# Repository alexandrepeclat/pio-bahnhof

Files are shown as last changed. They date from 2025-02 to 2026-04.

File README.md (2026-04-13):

### TODO SOFTWARE :

```
TODO MQTT + HomeAssistant ?
TODO virer les deps inutiles (CRC32 utilisé par librairie)
 TODO voir pour les conflits avec dépendances de command-library
 TODO réorganiser la détection d'erreurs.
- on a emergencyStop et assertThis un peu interchangeables
- on a des checks sur des getters ou à des moments dans la logique du code et dans les fonctions dédiées...
- le state, flag et message sont un peu redondants
 TODO passer les strings en mémoire flash plutôt qu'en RAM 
 TODO s'assurer que tous les "getters" utilisés notamment dans les debug ne change pas les états ou valeurs :-)
 TODO Vérifier les valeurs passées depuis l'api un peu mieux en terme de limites
 TODO sécuriser API ?
```

### Flash to board

- Flash the software : `pio run --target upload`
- Flash static html file : `pio run --target uploadfs`

### Setting up the pulse offset

- Do manual calibration
- Set default panel as the actual panel
    - You should have the same panel on the device and UI
- Move pulse by pulse until the panel changes on the device
    - You may have a different panel on the device and UI
- Tune the pulse offset until both device and UI are on the same panel
    - If the UI shows the next panel : increase pulse offset
    - If the UI shows the previous panel : decrease pulse offset
- Save the settings !

### Hardware

| Ref | Description | V(in) | V(out) | Datasheet |
| --- | --- | --- | --- | --- |
| LM2596 | Step-down voltage regulator (Buck converter) | 7-30V | 5.2V | https://www.ti.com/product/LM2596 |
| NodeMCU v3 | ESP8266 module | 5-9V | | https://github.com/nodemcu/nodemcu-devkit-v3.0 |
| 38S6G5 | Optical encoder (360 steps/rev * 4 pulses) | 5-24V | | https://www.mantech.co.za/Datasheets/Products/e38s_jz-yeba.pdf |
| MG996R | Continuous rotation servo motor | 4.8-6.6V | | https://www.towerpro.com.tw/product/mg996r |
| KY-010 | Optical sensor | 3.3-5V | | https://sensorkit.joy-it.net/fr/sensorsky-010 |

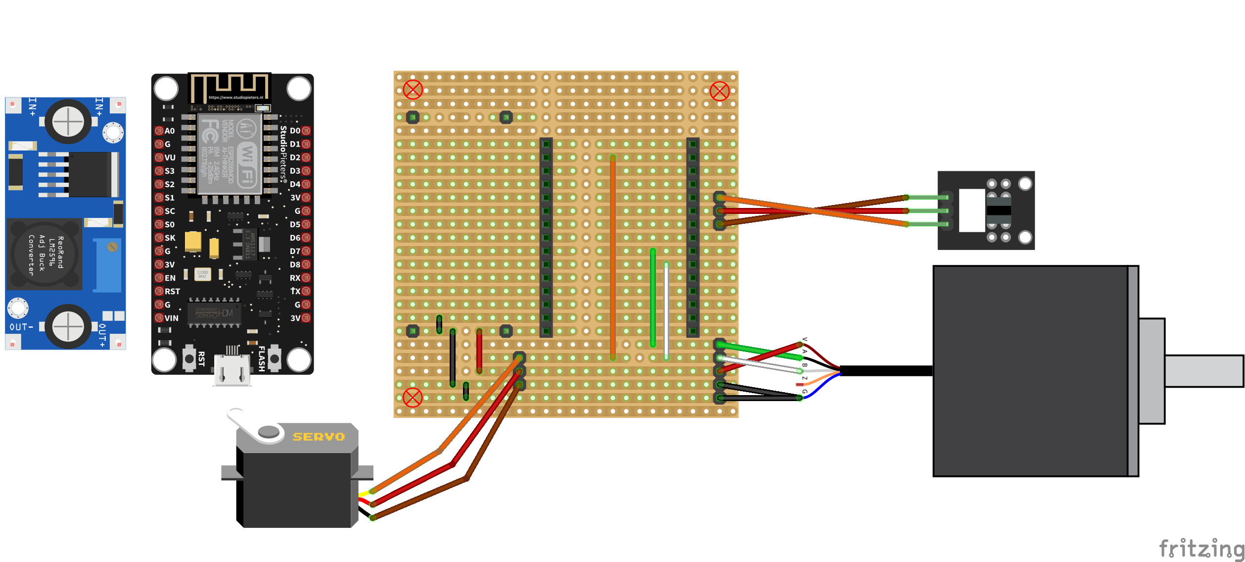
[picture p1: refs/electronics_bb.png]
Breadboard scheme

Electro scheme

### Mechanical stuff

https://geargenerator.com/beta/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

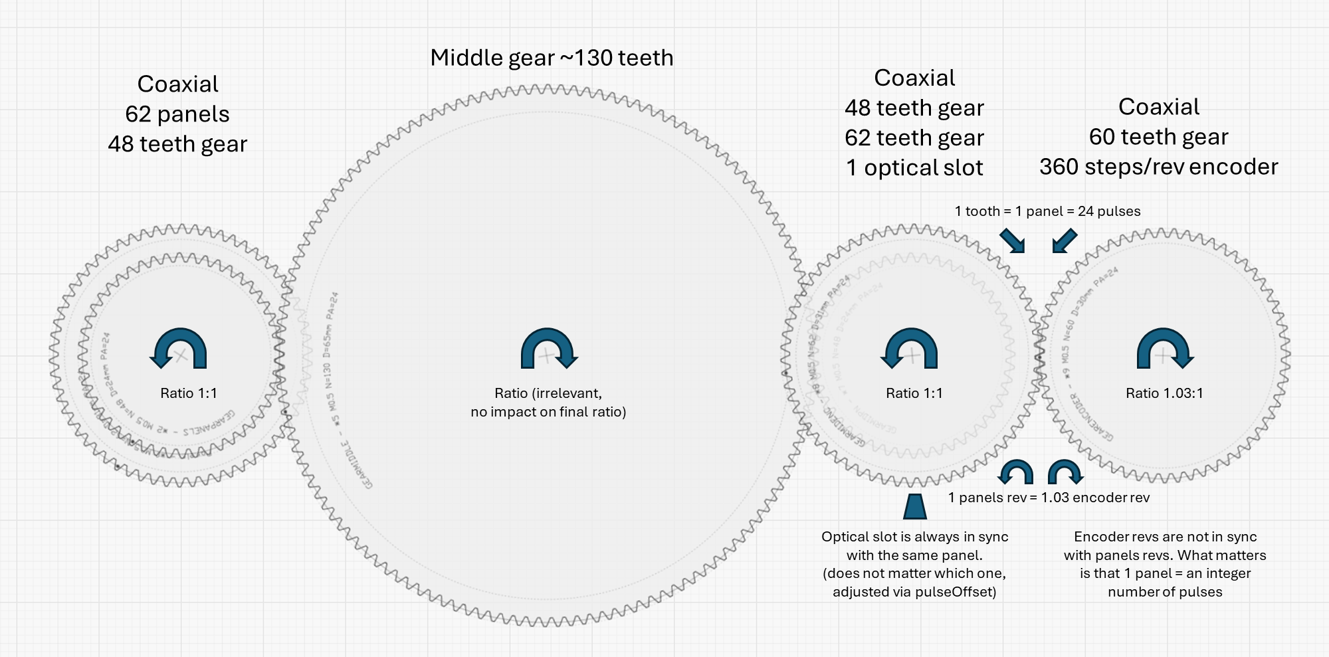
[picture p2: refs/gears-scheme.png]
Gears scheme


> Notes : 
>
> - Pulses number / panel must be an integer. This is why we have "clean" number of teeth for both gears, related to what is connected to them : 
> - 62 teeth for panels (divisor of 62 panels, but could be 31, 124...)
> - 60 teeth for encoder (divisor of 360 steps, but could be 36, 40, 72)
> - The actual pulses number per panel is `360 steps / rev * 4 pulses / step * (1 / 60 rev) = 24 pulses / panel`
> - However we do not need to have 1 panels full revolution to be equal to 1 encoder revolution
> - The actual encoder speed is `60/62 = 0.96` of the panels speed 
> - For each panels full revolution, we have `62/60 = 1.0333` encoder revolutions

### REST call examples

```
curl -Method Get -Uri "http://192.168.0.222/stop"
curl -Method Get -Uri "http://192.168.0.222/panel"
curl -Method Post -Uri "http://192.168.0.222/moveToPanel" -Body @{panel=6} -ContentType "application/x-www-form-urlencoded"
curl -Method Post -Uri "http://192.168.0.222/advancePanels" -Body @{count=2} -ContentType "application/x-www-form-urlencoded"
curl -Method Post -Uri "http://192.168.0.222/setCurrentPanel" -Body @{panel=0} -ContentType "application/x-www-form-urlencoded"
```

### Useful doc

- Split flap wall decoration SBB/CFF : https://commerce.sbb.ch/en/split-flap-display-wall-decoration-different-special-trains-1100.html
- Projet split flap diy : https://github.com/davidkingsman/split-flap
- Lib encoder esp32 (multi modes dont quadrature, avec interruptions) : https:github.com/madhephaestus/ESP32Encoder 
- Exemple encoder (pas quadrature mais directionnel) : https:github.com/sandy9159/How-to-connect-optical-rotary-encoder-with-Arduino
- Lib encodeur RPi Pico : https://github.com/GitJer/Some_RPI-Pico_stuff/tree/main/Rotary_encoder
- Lib encodeur interruptions : https://github.com/gfvalvo/NewEncoder/tree/master
- Connexion encodeur optique esp32 : https://electricdiylab.com/how-to-connect-optical-encoder-with-esp32/#Wiring_of_Optical_encoder_and_ESP32
- Thread sur lecture encodeur rapide : https://forum.arduino.cc/t/arduino-and-high-speed-rotary-encoders/327931/7
- Thread lecture encodeur state table : https://forum.arduino.cc/t/reading-a-quad-encoder-and-converting-to-a-function/272506/2
- Thread encodeur interruptions : https://stackoverflow.com/questions/51297371/arduino-rpm-code-with-quadrature-encoder-600ppr

### Shitty issues 

- Optical encoder 38s6g5 needs >= 5V https://forum.arduino.cc/t/fyi-interfacing-e38s6g5-600b-g24n-600p-r-rotary-encoder/1057892
- noInterrupt() et interrupt() pas utilisés car perturbent la lecture Serial et serveur HTTP. En principe on en a pas besoin car les variables volatiles sont <= 32 bits donc atomiques sur ESP8266.
- EEPROM.read() and EEPROM.write() only work with 1 single byte. Need to use EEPROM.get() / EEPROM.set() for int.

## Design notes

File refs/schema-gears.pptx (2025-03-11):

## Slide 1

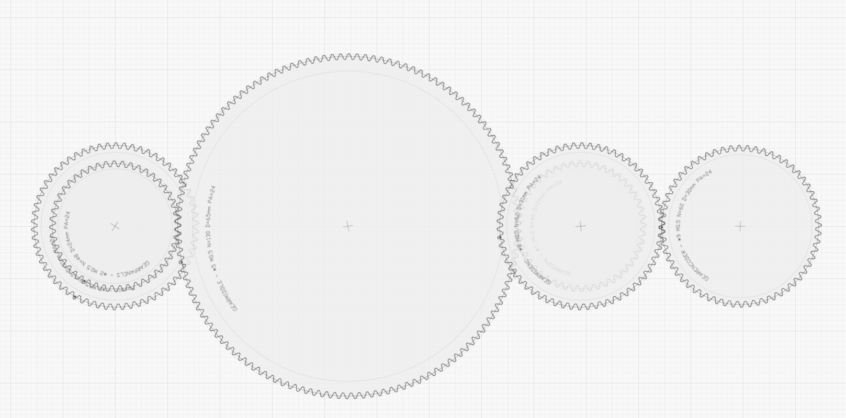
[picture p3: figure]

Coaxial
62 panels
48 teeth gear

Middle gear ~130 teeth

Coaxial
48 teeth gear
62 teeth gear
1 optical slot

Coaxial
60 teeth gear
360 steps/rev encoder

1 tooth = 1 panel = 24 pulses

Ratio 1:1

Ratio 1:1

Ratio (irrelevant,
no impact on final ratio)

Ratio 1.03:1

1 panels rev = 1.03 encoder rev

Optical slot is always in sync with the same panel.
(does not matter which one, adjusted via pulseOffset)

Encoder revs are not in sync with panels revs. What matters is that 1 panel = an integer number of pulses

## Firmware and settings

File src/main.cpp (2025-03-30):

#define DEBUG_ENABLED

#include <DebugBuilder.h>
#include <EEPROM.h>
#include <ESP8266WiFi.h>
#include <ESP8266mDNS.h>
#include <ESPAsyncWebServer.h>
#include <JsonSettingsBase.h>
#include <LittleFS.h>
#include <RestCommandHandler.h>
#include <SerialCommandHandler.h>
#include <Servo.h>
#include <secrets.h>

enum AppState {

  /**
   * Stopped state after an issue is detected.
   */
  EMERGENCY_STOPPED,

  /**
   * Normal stopped (idle) state.
   */
  STOPPED,

  /**
   * Auto-calibrating. Will move to target panel afterward.
   */
  AUTO_CALIBRATING,

  /**
   * Manually calibrating. Will stop afterward.
   */
  CALIBRATING,

  /**
   * Moving to target panel at normal speed.
   * Will auto-calibrate if not already done, then return to this state.
   * Will stop when target is reached.
   */
  MOVING_TO_TARGET,

  /**
   * Moving to target panel at slow speed.
   * Will not try to auto-calibrate.
   * Will stop when target is reached.
   * Used for settings adjustments or debugging.
   */
  MOVING_TO_TARGET_SLOW,
};

// Prototypes declaration
int getCurrentPulse();  // TODO réorganiser les fonctions dans un ordre correct
int getCurrentPanel();
int getTargetPulse();
float calculateSpeedMovingToTarget();
int getRemainingPulses();
void setMotorSpeed(float normalizedSpeed);
void setTargetPanel(int panel);
int getTargetPanel();
void emergencyStop(String message);
String stateToString(AppState state);
void setCurrentState(AppState newState);
int getDefaultPanel();
int getDefaultPulseOffset();
int getCurrentRpm();
float normalizeSpeed(int speed);
int denormalizeSpeed(float normalizedSpeed);
int computePulsesForwardDistance(int from, int to);
int computePulsesMinDistance(int from, int to);
int computeRpm(int lastPulse, int currentPulse, unsigned long lastTime, unsigned long currentTime);

#define DEBUG_ENABLED

// Pins configuration
#define SERVO_PIN D1      // Orange
#define ENCODER_PIN_A D6  // Green
#define ENCODER_PIN_B D7  // White
#define OPTICAL_PIN D4    // Orange

// Connections
AsyncWebServer server(80);  // For REST API calls
AsyncCorsMiddleware cors;
AsyncWebSocket ws("/panel");  // For notifying clients of panel changes
SerialCommandHandler serialCommandHandler;
RestCommandHandler restCommandHandler(server);

// App state
volatile AppState currentState = STOPPED;
bool errorFlag = false;      // Emergency stop flag
String errorMessage = "";    // Emergency stop message
bool criticalError = false;  // Error preventing the device from running //TODO merger avec errorFlag ?
volatile bool calibrated = false;

// Panels and pulses
const int PANELS_COUNT = 62;
const int PULSES_PER_PANEL = 24;                           // ENCODER_RESOLUTION / ENCODER_GEAR_TEETH * ENCODER_PULSES_PER_STEP = 360 / 60 * 4 = 24
const int PULSES_COUNT = PANELS_COUNT * PULSES_PER_PANEL;
const int TARGET_PULSE_OFFSET = 12;                        // When setting a target panel, use the nth pulse of this panel for centering //TODO à voir si configurable (et vitesse aussi car dépend de elle)
static_assert(TARGET_PULSE_OFFSET >= 0 && TARGET_PULSE_OFFSET < PULSES_PER_PANEL, "OFFSET must be in range [0-PULSES_PER_PANEL]");

// Encoder
const int8_t ENCODER_DIRECTION_SIGN = 1; // 1 for normal direction, -1 for reverse (depends on AB wiring)
const int8_t ENCODER_STATE_TABLE[16] = {0, 1, -1, -0, -1, 0, -0, 1, 1, -0, 0, -1, -0, -1, 1, 0};  // Encoder state table for natural debouncing (-0 are non valid states)
int targetPulse = 0;
volatile int encoderPulsesRaw = 0;

// Optical sensor
const int OPTICAL_DETECTED_EDGE = RISING;  // Optical is 0 on slot (detected) and 1 when signal cut by wheel body
volatile bool opticalState = HIGH;         // Assume not on slot at start (will be updated on 1st loop)

// Servo
Servo servo;
const int STOP_SPEED = 90;  
const int RUN_SPEED = 140;  // Servo max forward speed [91-180] (140 is quite good, 6 sec for 1 revolution)
static_assert(RUN_SPEED > 90, "RUN_SPEED must be greater than 90 or everything will break !");

/**
 * Configurable settings stored in flash memory.
 * Values can be preset by flashing a settings.json file on the ESP.
 */
class Settings : public JsonSettingsBase {
 public:
  int defaultPulse = 0;     // Default pulse for the device : 0
  String mdnsName = "cff";  // Default MDNS name for the device : cff.local

  Settings()
      : JsonSettingsBase("/settings.json") {}

  void serialize(JsonDocument& doc) override {
    doc["defaultPulse"] = defaultPulse;
    doc["mdnsName"] = mdnsName;
  }

  void deserialize(JsonDocument& doc) override {
    defaultPulse = doc["defaultPulse"] | defaultPulse;
    mdnsName = doc["mdnsName"] | mdnsName;
  }
};
Settings settings;

/**
 * Debug fields are displayed via serial and can be queried via REST API.
 * (fields with parameter "true" trigger a serial print when they change)
 */
std::vector<DebugField> debugFields = {
    {"currentPanel", false, [] { return getCurrentPanel(); }},
    {"currentPulse", true, [] { return getCurrentPulse(); }},
    {"targetPanel", false, [] { return getTargetPanel(); }},
    {"targetPulse", true, [] { return getTargetPulse(); }},
    {"optical", true, [] { return opticalState; }},
    {"calibrated", true, [] { return calibrated; }},
    {"dist", false, [] { return getRemainingPulses(); }},
    {"servo", true, [] { return servo.read(); }},  // TODO à voir parfois une valeur ne change pas mais le hash est différent (se produit dans les états ou le servo tourne)
    {"dfltPulse", true, [] { return settings.defaultPulse; }},
    {"dfltPanel", false, [] { return getDefaultPanel(); }},
    {"dfltPulseOffset", false, [] { return getDefaultPulseOffset(); }},
    {"rpm", false, [] { return getCurrentRpm(); }},
    {"encPulsesRaw", false, [] { return encoderPulsesRaw; }},
    {"wsClients", true, [] { return ws.count(); }},
    {"state", true, [] { return stateToString(currentState); }},
    {"errorMessage", true, [] { return errorMessage; }},
};
DebugBuilder debugBuilder(debugFields);

void assertError(bool condition, const std::function<String()>& messageBuilder) {
  if (!condition) {
    emergencyStop(messageBuilder());
  }
}

void assertWarn(bool condition, const std::function<String()>& messageBuilder) {
  if (!condition) {
    errorMessage = messageBuilder();
  }
}

void emergencyStop(String message) {
  servo.write(STOP_SPEED);  // First things first, stop the motor
  errorFlag = true;         // Error flag will prevent the motor to run, until manually reset
  setCurrentState(EMERGENCY_STOPPED);
  errorMessage = message;
}

String stateToString(AppState state) {
  switch (state) {
    case EMERGENCY_STOPPED:
      return "EMERGENCY_STOPPED";
    case STOPPED:
      return "STOPPED";
    case CALIBRATING:
      return "CALIBRATING";
    case AUTO_CALIBRATING:
      return "AUTO_CALIBRATING";
    case MOVING_TO_TARGET:
      return "MOVING_TO_TARGET";
    case MOVING_TO_TARGET_SLOW:
      return "MOVING_TO_TARGET_SLOW";
  }
  return "UNKNOWN_STATE";  // Not reachable
}

void setCurrentState(AppState newState) {
  currentState = newState;
}

int IRAM_ATTR getCurrentPulse() {
  return (encoderPulsesRaw + settings.defaultPulse) % PULSES_COUNT;
}

void setTargetPulse(int pulse) {
  assertError(pulse >= 0 && pulse < PULSES_COUNT, [pulse] { return "pulse " + String(pulse) + " out of bounds"; });
  targetPulse = pulse;
}

int getTargetPulse() {
  return targetPulse;
}

int getCurrentPanel() {
  return getCurrentPulse() / PULSES_PER_PANEL;
}

int getTargetPanel() {
  return targetPulse / PULSES_PER_PANEL;
}

void setTargetPanel(int panel) {
  assertError(panel < PANELS_COUNT, [panel] { return "panel " + String(panel) + " > " + PANELS_COUNT; });
  setTargetPulse((panel * PULSES_PER_PANEL) + TARGET_PULSE_OFFSET);
}

int getDefaultPanel() {
  return settings.defaultPulse / PULSES_PER_PANEL;
}

int getDefaultPulseOffset() {
  return settings.defaultPulse % PULSES_PER_PANEL;
}

/**
 * Compute the distance between two pulses, only in forward direction.
 */
int IRAM_ATTR computePulsesForwardDistance(int from, int to) {
  return (to - from + PULSES_COUNT) % PULSES_COUNT;
}

/**
 * Compute the minimum distance between two pulses, either forward or backward.
 */
int IRAM_ATTR computePulsesMinDistance(int from, int to) {
  int distance = computePulsesForwardDistance(from, to);
  return min(distance, PULSES_COUNT - distance);
}

int getRemainingPulses() {
  int currentPulse = getCurrentPulse();
  return computePulsesForwardDistance(currentPulse, targetPulse);
}

int getCurrentRpm() {
  static int lastPulse = 0;
  static unsigned long lastTime = 0;
  int currentPulse = getCurrentPulse();
  unsigned long currentTime = millis();
  int rpm = computeRpm(lastPulse, currentPulse, lastTime, currentTime);
  lastPulse = currentPulse;
  lastTime = currentTime;
  return rpm;
}

int computeRpm(int lastPulse, int currentPulse, unsigned long lastTime, unsigned long currentTime) {
  unsigned long elapsedTime = currentTime - lastTime;
  if (elapsedTime == 0)
    return 0;  // Avoid divide by 0
  int pulsesDelta = computePulsesForwardDistance(lastPulse, currentPulse);
  return (pulsesDelta * 60000.0) / (elapsedTime * PULSES_COUNT);
}

/**
 * Securely set the motor speed within boundaries, based on normalized value.
 * Will set the motor to STOP_SPEED if an error was raised.
 * @param normalizedSpeed The speed value between 0 and 1
 */
void setMotorSpeed(float normalizedSpeed) {
  // If error was raised, stop the motor
  if (errorFlag) {
    servo.write(STOP_SPEED);
    return;
  }

  // Constrain normalized speed and map it to servo speed values
  normalizedSpeed = constrain(normalizedSpeed, 0.f, 1.f);
  int speed = denormalizeSpeed(normalizedSpeed);
  if (servo.read() != speed) {
    servo.write(speed);  // Skip if speed did not change (~20ms)
  }
}

/**
 * Normalize a speed value between STOP_SPEED and RUN_SPEED to a value between 0 and 1.
 */
float normalizeSpeed(int speed) {
  return map(speed, STOP_SPEED, RUN_SPEED, 0, 100) / 100.f;
}

/**
 * Denormalize a speed value between 0 and 1 to a value between STOP_SPEED and RUN_SPEED.
 */
int denormalizeSpeed(float normalizedSpeed) {
  return map(normalizedSpeed * 100, 0, 100, STOP_SPEED, RUN_SPEED);
}

// Commands called by serial or REST API

String doGetRestRoutes() {
  return restCommandHandler.getRoutesList();
}

String doGetSerialCommands() {
  return serialCommandHandler.getCommandsList();
}

String doSetDefaultPulse(int pulse) {
  if (pulse < 0 || pulse >= PULSES_COUNT) {
    return "Error: default pulse " + String(pulse) + " out of bounds [0-" + String(PULSES_COUNT) + "]";
  }
  settings.defaultPulse = pulse;
  return "Default pulse set to " + String(settings.defaultPulse) + ". Default panel is " + String(getDefaultPanel()) + " with offset " + String(getDefaultPulseOffset());
}

String doSetDefaultPanelAndOffset(int panel, int offset) {
  if (panel < 0 || panel >= PANELS_COUNT) {
    return "Error: default panel " + String(panel) + " out of bounds [0-" + String(PANELS_COUNT) + "]";
  }
  if (offset < 0 || offset >= PULSES_PER_PANEL) {
    return "Error: default offset " + String(offset) + " out of bounds [0-" + String(PULSES_PER_PANEL) + "]";  // TODO fonction pour checks bounds homogène
  }
  settings.defaultPulse = panel * PULSES_PER_PANEL + offset;
  return "Default pulse set to " + String(settings.defaultPulse) + ". Default panel is " + String(getDefaultPanel()) + " with offset " + String(getDefaultPulseOffset());
}

String doSaveSettings() {
  settings.save();
  return "Settings saved: " + settings.getContent();
}

String doLoadSettings() {
  settings.load();
  return "Settings loaded: " + settings.getContent();
}

String doGetDebug() {
  return debugBuilder.buildJson();
}

String doGetCurrentPanel() {
  return String(getCurrentPanel());
}

String doMoveToPanel(int panel) {
  if (panel >= PANELS_COUNT) {
    return "Panel " + String(panel) + " out of bounds [0-" + String(PANELS_COUNT) + "]";
  }
  setTargetPanel(panel);
  setCurrentState(MOVING_TO_TARGET);
  return "Moving to panel " + String(getTargetPanel());
}

String doAdvancePanels(int count) {
  int currentPanel = getCurrentPanel();
  setTargetPanel((currentPanel + count) % PANELS_COUNT);
  setCurrentState(MOVING_TO_TARGET);
  return "From " + String(currentPanel) + ", Advancing " + String(count) + " panels to " + String(getTargetPanel());
}

String doAdvancePulses(int pulseCount) {
  int currentPulse = getCurrentPulse();
  setTargetPulse((currentPulse + pulseCount) % PULSES_COUNT);
  setCurrentState(MOVING_TO_TARGET_SLOW);
  return "Advancing " + String(pulseCount) + " pulses to " + String(targetPulse);
}

String doCalibrate() {
  calibrated = false;
  setTargetPanel(0);  // After on-demand calibration, will go to panel 0
  setCurrentState(CALIBRATING);
  return "Calibration started. Rotating until optical sensor edge is detected.";
}

String doStop() {
  setMotorSpeed(0);
  setCurrentState(STOPPED);
  setTargetPulse(getCurrentPulse());  // Consider target as reached
  return "Stopped. Current panel set to " + String(getCurrentPanel());
}

String doReset() {
  setMotorSpeed(0);  // Set everything as stopped
  setCurrentState(STOPPED);
  calibrated = false;  // Reset all flags
  errorFlag = false;
  errorMessage = "";
  settings.load();  // Reload settings
  return "Reset";
}

float calculateSpeedCalibration() {
  if (OPTICAL_DETECTED_EDGE == RISING) {
    return opticalState == LOW ? 0.3f : 1.f;  // Half speed when we are about to detect the 2nd edge
  } else {
    return opticalState == HIGH ? 0.3f : 1.f;
  }
}

float calculateSpeedMovingToTarget() {
  int remainingPulses = getRemainingPulses();
  if (remainingPulses == 0) {
    return 0.f;  // Stop if target is reached (should be already stopped by encoder interrupt)
  } else if (remainingPulses <= PULSES_PER_PANEL) {
    return 0.3f;  // Slow down as we approach target
  } else if (remainingPulses <= PULSES_PER_PANEL * 2) {
    return 0.5f;
  } else if (remainingPulses <= PULSES_PER_PANEL * 3) {
    return 0.7f;
  } else {
    return 1.0f;  // Constant speed accross all panels
  }
}

float calculateSpeedMovingToTargetSlow() {
  return 0.15f;
}

/**
 * Make state transitions based on current state and conditions
 * ! The currentState is the only variable that should be modified in this function !
 */
void evaluateStateTransitions() {
  switch (currentState) {
    case EMERGENCY_STOPPED:
    case STOPPED:
      // Nothing to do, wait for command
      break;
    case CALIBRATING: {
      if (calibrated) {
        setCurrentState(STOPPED);
      }
      break;
    }
    case AUTO_CALIBRATING: {
      if (calibrated) {
        setCurrentState(MOVING_TO_TARGET);
      }
      break;
    }
    case MOVING_TO_TARGET: {
      if (!calibrated) {
        setCurrentState(AUTO_CALIBRATING);
      }
      if (getRemainingPulses() == 0) {
        setCurrentState(STOPPED);
      }
      break;
    }
    case MOVING_TO_TARGET_SLOW: {
      if (getRemainingPulses() == 0) {
        setCurrentState(STOPPED);
      }
      break;
    }
  }
}

void processStateActions() {
  switch (currentState) {
    case EMERGENCY_STOPPED:
    case STOPPED:
      setMotorSpeed(0);
      break;
    case CALIBRATING:
    case AUTO_CALIBRATING: {
      float speed = calculateSpeedCalibration();
      setMotorSpeed(speed);
      break;
    }
    case MOVING_TO_TARGET: {
      float speed = calculateSpeedMovingToTarget();
      setMotorSpeed(speed);
    } break;
    case MOVING_TO_TARGET_SLOW: {
      float speed = calculateSpeedMovingToTargetSlow();
      setMotorSpeed(speed);
      break;
    }
  }
}

void readSensors() {
  opticalState = digitalRead(OPTICAL_PIN);
}

void connectToWiFi() {
  if (WiFi.status() != WL_CONNECTED) {
    setMotorSpeed(0);  // Stop the motor if we are offline
    WiFi.disconnect();
    WiFi.begin(WIFI_SSID, WIFI_PASSWORD);
    while (WiFi.status() != WL_CONNECTED) {
      delay(1000);
      Serial.println("Connecting to WiFi " + WiFi.SSID() + "...");
    }
    Serial.println("✅ Connected to WiFi " + WiFi.SSID() + " IP Address: " + WiFi.localIP().toString() + " RSSI: " + WiFi.RSSI());
  }
}

/**
 * Check for errors during motor operation such as blockages or speed out of bounds.
 */
void checkForRunningErrors() {
  int motorSpeed = servo.read();

  // TODO Check for blockages

  // Detect motor speed out of bounds
  if (motorSpeed < 90) {
    emergencyStop("Motor speed should not be lower than 90");
  } else if (motorSpeed > 180) {
    emergencyStop("Motor speed should not be greater than 180");
  }
}

void IRAM_ATTR handleEncoderInterrupt() {  // 4us

  // Read encoder pins and update the pulses count
  static uint8_t encoderState = 0;
  byte pinA = (GPIO_REG_READ(GPIO_IN_ADDRESS) >> ENCODER_PIN_A) & 1;
  byte pinB = (GPIO_REG_READ(GPIO_IN_ADDRESS) >> ENCODER_PIN_B) & 1;
  encoderState = ((encoderState << 2) | (pinA << 1) | pinB) & 15;  // Décale et masque les bits
  int8_t pulseInc = ENCODER_STATE_TABLE[encoderState] * ENCODER_DIRECTION_SIGN;
  encoderPulsesRaw += pulseInc;

  // Stop here if the encoder did not move forward
  if (pulseInc < 1)
    return;

  // Check if the optical sensor detected the edge
  // If so, zero the encoder + consider calibration as done
  static bool opticalLastState = HIGH;  // Initialize to HIGH (not detected)
  opticalState = (GPIO_REG_READ(GPIO_IN_ADDRESS) >> OPTICAL_PIN) & 1;
  if ((OPTICAL_DETECTED_EDGE == RISING && opticalLastState == LOW && opticalState == HIGH) ||
      (OPTICAL_DETECTED_EDGE == FALLING && opticalLastState == HIGH && opticalState == LOW)) {
    assertWarn(!calibrated || computePulsesMinDistance(0, encoderPulsesRaw) <= 1, [] {
      return "Missing steps... Optical edge detected at pulse " + String(getCurrentPulse()) + " instead of " + String(settings.defaultPulse);
    });
    encoderPulsesRaw = 0;
    calibrated = true;
  }
  opticalLastState = opticalState;

  // Check if the target is reached
  // Note: cannot be done in main loop because the motor can overshoot the target before the loop is executed
  if ((currentState == MOVING_TO_TARGET || currentState == MOVING_TO_TARGET_SLOW) && targetPulse == getCurrentPulse()) {
    currentState = STOPPED;
  }
}

/**
 * Notify websocket clients on panel changes.
 */
void notifyPanelChanges() {
  static int lastPanel = -1;
  int currentPanel = getCurrentPanel();
  if (currentPanel != lastPanel) {
    ws.textAll(String(currentPanel));
    lastPanel = currentPanel;
  }
}
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
void loop() {
  if (criticalError) {
    delay(1000);
    return;
  }

  // Keep connections alive
  connectToWiFi();  // TODO Wifi non bloquant + voir si problèmes en cas de déconnexion avec le serveur http ou autre
  MDNS.update();

  // Keep things running
  readSensors();
  evaluateStateTransitions();  // Decide next transition if any
  processStateActions();       // Set behavior based on current state
  checkForRunningErrors();     // Check for blockages and co

  // Handle commands and notifications to clients
  serialCommandHandler.handleSerial();
  restCommandHandler.handleClient();
  notifyPanelChanges();

  // Print debug info if something's new
#ifdef DEBUG_ENABLED
  if (debugBuilder.hasChanged()) {  // 110 us
    Serial.println(debugBuilder.buildJson());
  }
#endif
}

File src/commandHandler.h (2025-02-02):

#include <Arduino.h>
#include <functional>
#include <map>
#include <sstream>
#include <string>
#include <type_traits>
#include <vector>

// Classe pour gérer l'enregistrement et l'appel des commandes
class CommandHandler {
 public:
  // Enregistrer une commande sans argument
  void registerCommand(const std::string& command, std::function<void()> callback) {
    _commandCallbacks[command] = [this, callback](const std::vector<std::string>& args) {
      Serial.println("args size: " + String(args.size()));
      if (!args.empty()) {
        Serial.println("Erreur: trop d'arguments.");
        return;
      }
      callback();
    };
  }

  // Enregistrer une commande avec 1 argument
  template <typename Arg1>
  void registerCommand(const std::string& command, std::function<void(Arg1)> callback) {
    _commandCallbacks[command] = [this, callback](const std::vector<std::string>& args) {
      if (args.size() != 1) {
        Serial.println("Erreur: mauvais nombre d'arguments.");
        return;
      }
      Arg1 arg1 = convertArgument<Arg1>(args[0]);  // Conversion
      callback(arg1);
    };
  }

  // Enregistrer une commande avec 2 arguments
  template <typename Arg1, typename Arg2>
  void registerCommand(const std::string& command, std::function<void(Arg1, Arg2)> callback) {
    _commandCallbacks[command] = [this, callback](const std::vector<std::string>& args) {
      if (args.size() != 2) {
        Serial.println("Erreur: mauvais nombre d'arguments.");
        return;
      }
      Arg1 arg1 = convertArgument<Arg1>(args[0]);  // Conversion
      Arg2 arg2 = convertArgument<Arg2>(args[1]);  // Conversion
      callback(arg1, arg2);
    };
  }

  // Enregistrer une commande avec 3 arguments
  template <typename Arg1, typename Arg2, typename Arg3>
  void registerCommand(const std::string& command, std::function<void(Arg1, Arg2, Arg3)> callback) {
    _commandCallbacks[command] = [this, callback](const std::vector<std::string>& args) {
      if (args.size() != 3) {
        Serial.println("Erreur: mauvais nombre d'arguments.");
        return;
      }
      Arg1 arg1 = convertArgument<Arg1>(args[0]);  // Conversion
      Arg2 arg2 = convertArgument<Arg2>(args[1]);  // Conversion
      Arg3 arg3 = convertArgument<Arg3>(args[2]);  // Conversion
      callback(arg1, arg2, arg3);
    };
  }

  // Gérer les commandes série
  void handleSerialCommands() {
    static String command = "";

    if (Serial.available() > 0) {
      String incomingChar = Serial.readString();  // Lire toute la chaîne d'entrée

      // If backspace is pressed remove the last character
      if (incomingChar == "\b") {
        if (command.length() > 0) {
          command.remove(command.length() - 1, 1);
        }
      } else {
        command += incomingChar;  // Ajouter le caractère à la commande
      }

      // Si la commande se termine par un retour à la ligne, on la traite
      if (command.endsWith("\n")) {
        processCommand(command);  // Traiter la commande complète
        command = "";             // Réinitialiser pour la prochaine commande
      }
    }
  }

 private:
  std::map<std::string, std::function<void(const std::vector<std::string>&)>> _commandCallbacks;

  // Traitement de la commande
  void processCommand(const String& commandStr) {
    std::istringstream iss(commandStr.c_str());
    std::vector<std::string> tokens;
    std::string token;

    while (iss >> token) {  // Découpe en mots en ignorant les espaces multiples
      tokens.push_back(token);
    }

    if (tokens.empty())
      return;  // Ignore les lignes vides

    std::string command = tokens[0];
    std::vector<std::string> args(tokens.begin() + 1, tokens.end());  // Récupère tous les arguments (éventuellement vide)

    auto it = _commandCallbacks.find(command);
    if (it != _commandCallbacks.end()) {
      it->second(args);  // Envoie une liste vide si pas d'arguments
    } else {
      Serial.println("Commande inconnue.");
    }
  }

  // Conversion des arguments en fonction de leur type
  template <typename T>
  T convertArgument(const std::string& arg) {
    if constexpr (std::is_same_v<T, int>) {
      return std::stoi(arg);
    } else if constexpr (std::is_same_v<T, float>) {
      return std::stof(arg);
    } else {
      return arg;  // pour le cas des strings
    }
  }
};

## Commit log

2025-01-08 code refactoré, plus clair, un seul compteur pour les panels
2025-01-09 normalized motor speed + security for no negative motor speed + motor stop flag
2025-01-09 calibration api
2025-01-10 corrections vitesse + offset
    [main.cpp]
2025-01-11 Update main.cpp
    corrections et améliorations optique front montant/descendant
    [main.cpp]
2025-01-19 Fonctions de sécurité à refactorer
2025-01-24 NEW encoder (working on it)
2025-01-24 Optique via interrupt OK
2025-01-24 encodeur avec interruption perso
2025-01-24 Gros bordel qui passe tout par interruptions à refactorer mais fonctionne super bien !
2025-01-25 Marche moyen (débug encoder)
2025-01-30 V4 new encoder gear
2025-02-01 Tentative de gestion centralisée rest + serial (trop dynamique)
2025-02-03 utilisation strings arduino
2025-02-13 update electro
    [electronics0.fzz]
2025-02-15 beau schéma !
    [electronics0 - Copie.fzz, electronics0.fzz, electronics0_back.fzz]
